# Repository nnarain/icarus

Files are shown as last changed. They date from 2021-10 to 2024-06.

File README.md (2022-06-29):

# Icarus Flight Controller




Icarus is a controller for robotics applications.

Firmware is located [here](https://github.com/nnarain/icarus-firmware).

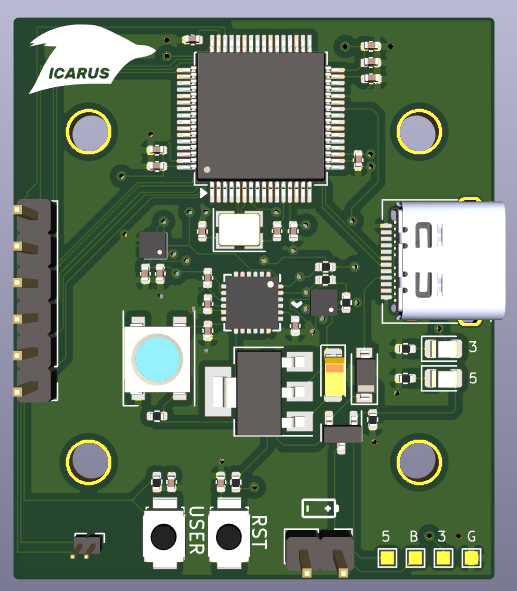
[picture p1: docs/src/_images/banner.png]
Image not found


Features:

* Controls 4 DC brushed motors
* IMU (gyro/accelerometer/temperature)
* Barometer
* USB Serial
* Battery sense
* 30.5 x 30.5 millimeter mounting holes (for drones).

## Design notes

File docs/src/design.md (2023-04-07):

# Design

Below is the design documentation for the Icarus Flight Controller.

Full schematics can be viewed here: {{#find schematic}}

# Scope

The scope of this project is to design and build an embedded system that can be used as a microquad flight controller.

| Priority | Item |
| --- | --- |
| Must | Support control of 4 motors |
| Must | Have motion sensing |
| Must | Interface for remote control |
| Should | Have USB 2.0 support |

# High-level Components

```d2
power: Power Supply {
    usb: USB
    usb.shape: parallelogram

    pwr: PWR Port
    pwr.shape: parallelogram

    reg: Voltage Regulator

    usb -> reg <- pwr
}

sensors: Sensors {
    imu: IMU
    baro: Barometer
    mag: Magnetometer
}

mcu: MCU {
    radio_bus: Radio Bus
    radio_bus.shape: parallelogram

    sensor_bus: Sensor Bus
    sensor_bus.shape: parallelogram

    core: Core
    core.shape: diamond

    pwm: PWM
    pwm.shape: parallelogram

    sensor_bus -> core {
        style.animated: true
    }
    radio_bus -> core {
        style.animated: true
    }
    core -> pwm {
        style.animated: true
    }
}

rf: Radio

rotors: Rotors
rotors.shape: parallelogram

power.reg -> sensors
power.reg -> mcu

rf -> mcu: Throttle {
    style.animated: true
}

mcu -> rf: Telemetry {
    style.animated: true
}

sensors.imu -> mcu: Accel / Gyro {
    style.animated: true
}
sensors.baro -> mcu: Altitude {
    style.animated: true
}
sensors.mag -> mcu: Orientation {
    style.animated: true
}

mcu.pwm -> rotors {
    style.animated: true
}
mcu.pwm -> rotors {
    style.animated: true
}
mcu.pwm -> rotors {
    style.animated: true
}
mcu.pwm -> rotors {
    style.animated: true
}

```

* PWM output to drive rotors
* An IMU can be used for motion sensing. At minimum a gyro and accelerometer would be required
* A magnetometer is needed to prevent yaw drift
* RC input would be require as input to the controller

# Power Supply

**Requirements**

Voltage should be able to handle up to a 3S (11.1V) LiPo for some flexibility in battery choice.

**Power Supply Inputs**

The board will have two inputs for power:

* Two pin input for direct battery connection
* 5V input from a USB connector

# Sensors

**Requirements**

As one of the purposes of this controller is for drones, understanding orientation in the air will be critical.

**Sensor Selection**

* MPU6050 for attitude estimation
* Magnetometer to prevent yaw drift (though not required)
* Barometer for altitude

# MCU

The MCU requirements for this project are pretty basic:

* 4 PWM outputs
* 1x I2C
* USB Serial support

And ESP32-C3-MINI-1 module was selected for the following reasons:

* Enough IO to control 4 motors
* I2C for sensors
* Built-in 2.4GHz radio support + antenna

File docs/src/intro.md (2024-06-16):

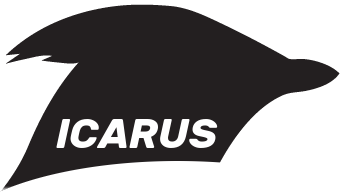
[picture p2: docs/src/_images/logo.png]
image not found!


Icarus is a flight controller for micro-quads.

Features:

* STM32F405 MCU
* IMU (gyro/accelerometer/temperature)
* Magnetometer
* Barometer
* USB 2.0
* 30.5 x 30.5 millimeter mounting pattern

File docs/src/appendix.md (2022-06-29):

# Appendix

| Document  | Item |
| --- | --- |
| Schematic | {{#find schematic}} |
| BOM | {{#find ibom}} |
| Fab Files | {{#find jlcpcb-files}} |

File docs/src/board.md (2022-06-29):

# Board

{{#find schematic-svg}}

{{#find render-top}}

{{#find render-bottom}}

{{#find render-3d}}

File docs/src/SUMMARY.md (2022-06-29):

# Summary

- [Introduction](./intro.md)
- [Design](./design.md)
- [Board](./board.md)
- [Appendix](./appendix.md)

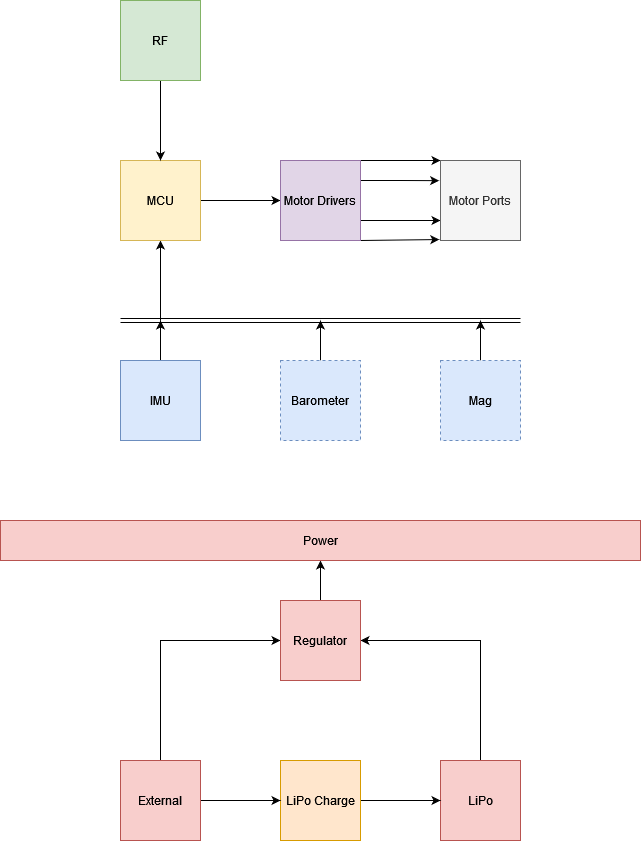
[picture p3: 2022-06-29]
docs/src/_images/highlevel-architecture.png

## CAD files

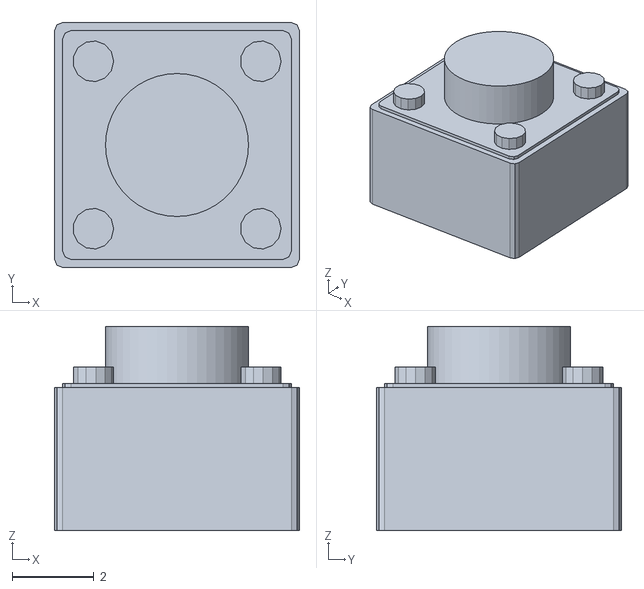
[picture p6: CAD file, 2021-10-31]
hardware/icarus/models/pushbutton_6mm.stl
6.00 x 6.00 x 5.00

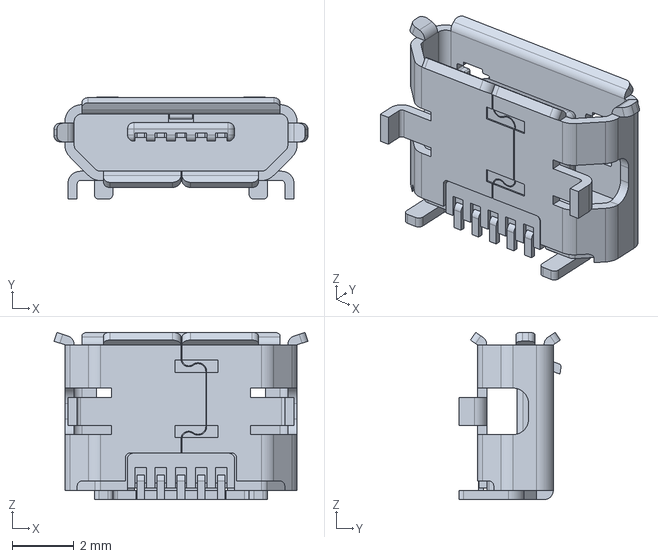
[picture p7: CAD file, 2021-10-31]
hardware/icarus/models/usb-b-micro-1050170001.stp
8.20 x 3.30 x 5.40 mm

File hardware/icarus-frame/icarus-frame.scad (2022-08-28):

// Simple frame for Icarus Flight Controller.
// Not intended to be consider robust (or good for that matter...)

base_dims = [43.084, 36.86, 3];
corners = [
    [base_dims[0] / 2, base_dims[1] / 2, 0],
    [-base_dims[0] / 2, base_dims[1] / 2, 0],
    [-base_dims[0] / 2, -base_dims[1] / 2, 0],
    [base_dims[0] / 2, -base_dims[1] / 2, 0]
];

mounting_hole_radius = 2.125;
mounting_hole_corner_offset = [
    [6.1, 3.429],
    [6.731, 3.429],
    [6.731, 3.175],
    [6.7, 3.1]
];

mounting_hole_positions = [
    [corners[0][0] - mounting_hole_corner_offset[0][0], corners[0][1] - mounting_hole_corner_offset[0][1]],
    [corners[1][0] + mounting_hole_corner_offset[1][0], corners[1][1] - mounting_hole_corner_offset[1][1]],
    [corners[2][0] + mounting_hole_corner_offset[2][0], corners[2][1] + mounting_hole_corner_offset[2][1]],
    [corners[3][0] - mounting_hole_corner_offset[3][0], corners[3][1] + mounting_hole_corner_offset[3][1]]
];

rotor_offsets = [6, 6];

rotor_positions = [
    [corners[0][0] + rotor_offsets[0], corners[0][1] + rotor_offsets[1]],
    [corners[1][0] - rotor_offsets[0], corners[1][1] + rotor_offsets[1]],
    [corners[2][0] - rotor_offsets[0], corners[2][1] - rotor_offsets[1]],
    [corners[3][0] + rotor_offsets[0], corners[3][1] - rotor_offsets[1]],
];

rotor_radius = 3;
rotor_wall_width = 2;
rotor_wall_clearance = 0.4;
rotor_mount_height = 15;
rotor_mount_wire_hole_radius = 2;
rotor_mount_bottom_thickness = 0.8;
rotor_mount_z_offset = 0.3;
strut_length = 10;
strut_thickness = base_dims[2];

battery_dims = [27, 16, 8.5];
battery_carriage_shell_thickness = 3;
battery_carriage_clearance = [1, 1, 2];
battery_carriage_dims = [
    battery_dims[0] + battery_carriage_clearance[0] + battery_carriage_shell_thickness,
    battery_dims[1] + battery_carriage_clearance[1] + battery_carriage_shell_thickness,
    battery_dims[2] + battery_carriage_clearance[2] + battery_carriage_shell_thickness
];
battery_cutout_dims = [
    battery_dims[0] + battery_carriage_clearance[0],
    battery_dims[1] + battery_carriage_clearance[1],
    battery_dims[2] + battery_carriage_clearance[2]
];

rotor_mount_radius = rotor_radius + rotor_wall_clearance + rotor_wall_width;


d = 0.01;

module rotor_mount() {
    z_offset = rotor_mount_z_offset * rotor_mount_height;

    difference() {
        union() {
            // Base rotor motor shape
            translate([0, 0, -z_offset]) 
                cylinder(r=rotor_mount_radius, h=rotor_mount_height, center=true, $fn=50);
            // Connective part of the main body
            translate([-strut_length / 2, 0, 0])
                cube(size=[strut_length, rotor_radius, strut_thickness], center=true);
        }
        union() {
            // Cutout space for the rotor
            translate([0, 0, rotor_mount_bottom_thickness - z_offset])
                cylinder(r=rotor_radius + rotor_wall_clearance, h=rotor_mount_height, center=true, $fn=50);
            translate([0, 0, -rotor_mount_height / 2 + d - z_offset])
                cylinder(r=rotor_mount_wire_hole_radius, h=rotor_mount_bottom_thickness * 2, center=true, $fn=100);
        }
    }
}

module battery_carriage() {
    difference() {
        cube(size=battery_carriage_dims, center=true);
        translate([battery_carriage_dims[0] / 2, 0, -d])
            cube(size=[battery_cutout_dims[0] * 2, battery_cutout_dims[1], battery_cutout_dims[2]], center=true);
    }
}

module base() {
    difference() {
        cube(size=base_dims, center=true);

        for (p = mounting_hole_positions) {
            translate([p[0], p[1], 0])
                cylinder(r=mounting_hole_radius, h=base_dims[2] * 2, center=true, $fn=100);
        }
    }
}

module frame() {
    union() {
        // Base where the controller is mounted
        base();

        // Battery Carriage
        translate([0, 0, -battery_carriage_dims[2] + battery_carriage_dims[2] / 2])
            battery_carriage();

        // Position rotor mounts
        for (i = [0:3]) {
            pos = rotor_positions[i];
            translate([pos[0], pos[1], 0])
                rotate([0, 0, 45 + (90 * i)])
                    rotor_mount();
        }
    }
    // rotor_mount();
}

frame();

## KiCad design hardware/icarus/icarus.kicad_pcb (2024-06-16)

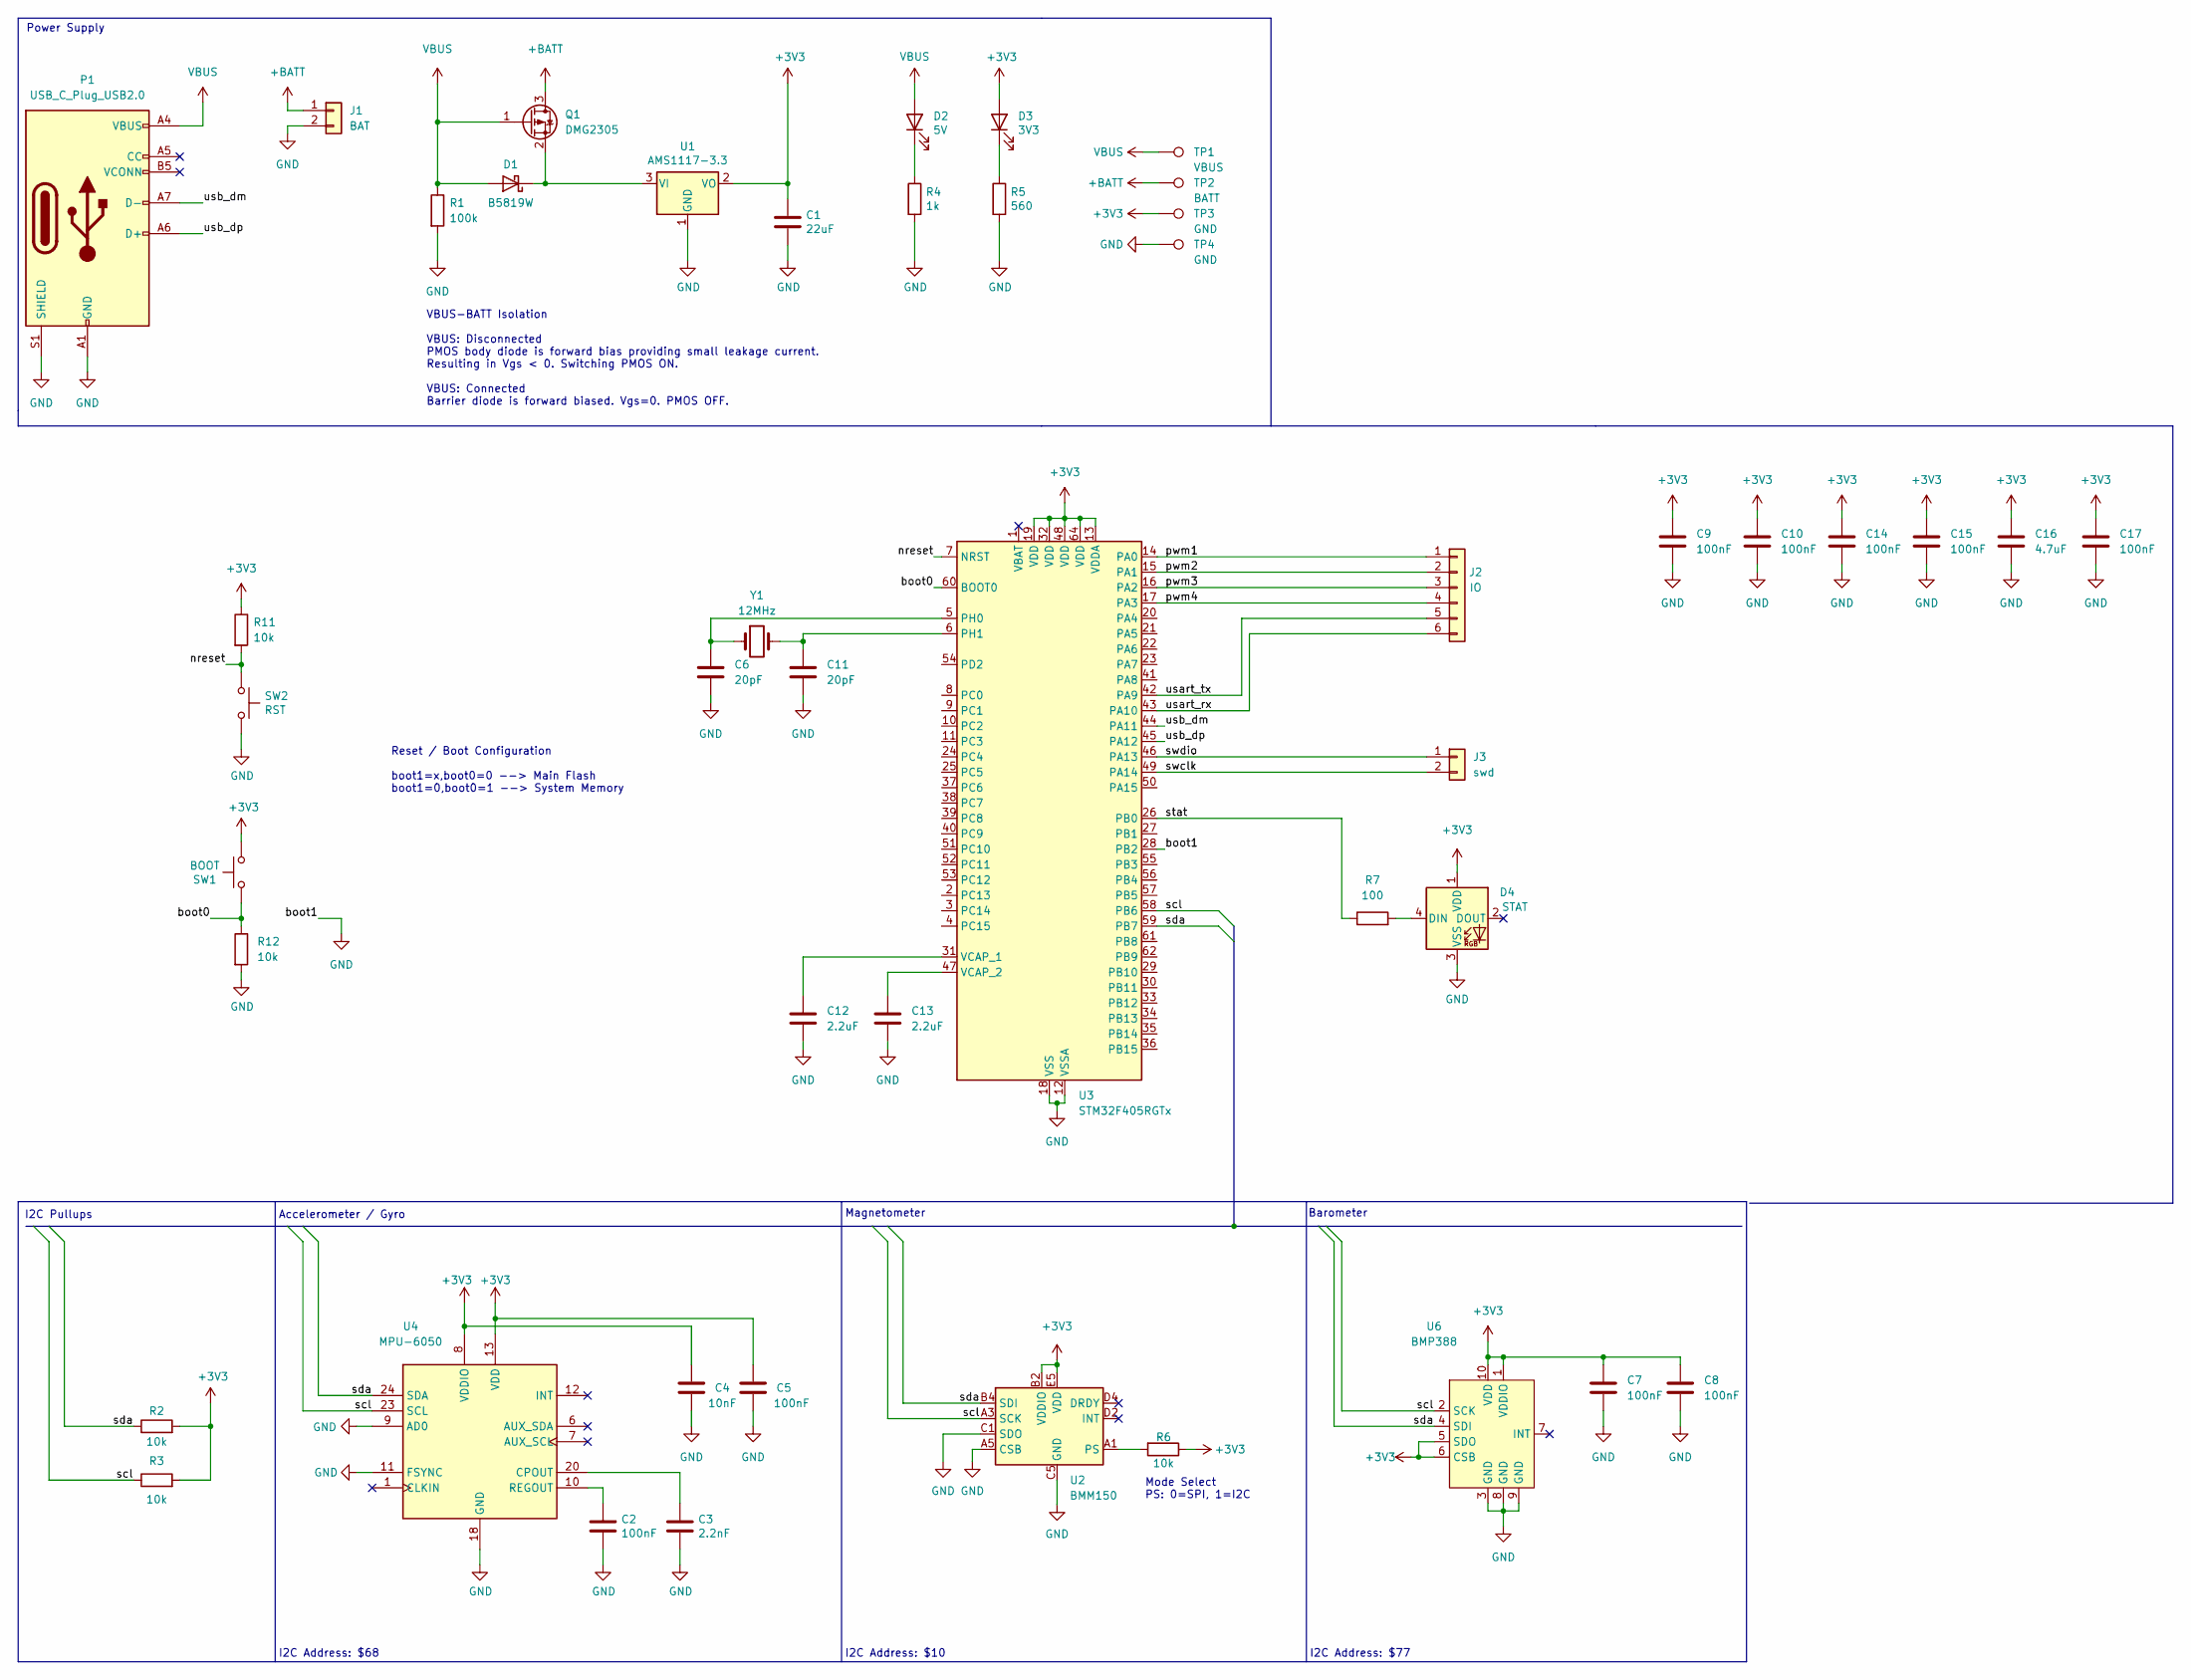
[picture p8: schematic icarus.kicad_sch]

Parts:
C1: 22uF; CP_EIA-3216-18_Kemet-A; LCSC C116575
C2, C5, C7, C8, C9, C10, C14, C15, C17: 100nF; C_0402_1005Metric; LCSC C307331
C3: 2.2nF; C_0402_1005Metric; LCSC C1531
C4: 10nF; C_0402_1005Metric; LCSC C15195
C6, C11: 20pF; C_0402_1005Metric; LCSC C1554
C12, C13: 2.2uF; C_0402_1005Metric; LCSC C12530
C16: 4.7uF; C_0402_1005Metric; LCSC C23733
D1: B5819W; D_SOD-123; LCSC C8598
D2: 5V; LED_0805_2012Metric; LCSC C434432
D3: 3V3; LED_0805_2012Metric; LCSC C434432
D4: STAT; LED_WS2812B_PLCC4_5.0x5.0mm_P3.2mm; LCSC C2761795
J1: BAT; PinHeader_1x02_P2.54mm_Vertical
J2: IO; PinHeader_1x06_P2.54mm_Vertical
J3: swd; PinHeader_1x02_P1.00mm_Vertical
P1: USB_C_Plug_USB2.0; TYPE-C-31-M-04; LCSC C129018
Q1: DMG2305; SOT-23; LCSC C150470
R1: 100k; R_0402_1005Metric; LCSC C25741
R2, R3, R6, R11, R12: 10k; R_0402_1005Metric; LCSC C25744
R4: 1k; R_0402_1005Metric; LCSC C25543
R5: 560; R_0402_1005Metric; LCSC C25172
R7: 100; R_0402_1005Metric; LCSC C25076
SW1: BOOT; TS-1088-AR02016; LCSC C720477
SW2: RST; TS-1088-AR02016; LCSC C720477
TP1: VBUS; TestPoint_Pad_1.0x1.0mm
TP2: BATT; TestPoint_Pad_1.0x1.0mm
TP3, TP4: GND; TestPoint_Pad_1.0x1.0mm
U1: AMS1117-3.3; SOT-223-3_TabPin2; LCSC C6186
U2: BMM150; WLCSP-12_1.56x1.56mm_P0.4mm; LCSC C171681
U3: STM32F405RGTx; LQFP-64_10x10mm_P0.5mm
U4: MPU-6050; InvenSense_QFN-24_4x4mm_P0.5mm; LCSC C24112
U6: BMP388; LCSC C779278
Y1: 12MHz; Crystal_SMD_3225-4Pin_3.2x2.5mm; LCSC C9002

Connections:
+3V3: C1.1, C4.2, C5.2, C7.1, C8.1, C9.1, C10.1, C14.1, C15.1, C16.1, C17.1, D3.2 (A), D4.1 (VDD), R2.2, R3.2, R6.1, R11.1, SW1.2, TP3.1, U1.2 (VO), U2.B2 (VDDIO), U2.E5 (VDD), U3.13 (VDDA), U3.19 (VDD), U3.32 (VDD), U3.48 (VDD), U3.64 (VDD), U4.8 (VDDIO), U4.13 (VDD), U6.1 (VDDIO), U6.5 (SDO), U6.6 (CSB), U6.10 (VDD)
+BATT: J1.1, Q1.3 (D), TP2.1
/boot0: R12.1, SW1.1, U3.60 (BOOT0)
/nreset: R11.2, SW2.1, U3.7 (NRST); also elsewhere on the board
/pwm1: J2.1, U3.14 (PA0)
/pwm2: J2.2, U3.15 (PA1)
/pwm3: J2.3, U3.16 (PA2)
/pwm4: J2.4, U3.17 (PA3)
/scl: R3.1, U2.A3 (SCK), U3.58 (PB6), U4.23 (SCL), U6.2 (SCK)
/sda: R2.1, U2.B4 (SDI), U3.59 (PB7), U4.24 (SDA), U6.4 (SDI)
/stat: R7.1, U3.26 (PB0)
/swclk: J3.2, U3.49 (PA14)
/swdio: J3.1, U3.46 (PA13)
/usart_rx: J2.6, U3.43 (PA10)
/usart_tx: J2.5, U3.42 (PA9)
/usb_dm: P1.A7 (D-), U3.44 (PA11)
/usb_dp: P1.A6 (D+), U3.45 (PA12)
GND: C1.2, C2.2, C3.2, C4.1, C5.1, C6.2, C7.2, C8.2, C9.2, C10.2, C11.2, C12.2, C13.2, C14.2, C15.2, C16.2, C17.2, D4.3 (VSS), J1.2, P1.A1 (GND), P1.A12 (GND), P1.B1 (GND), P1.B12 (GND), P1.S1 (SHIELD), R1.2, R4.2, R5.2, R12.2, SW2.2, TP4.1, U1.1 (GND), U2.A5 (CSB), U2.C1 (SDO), U2.C5 (GND), U2.E1 (GND), U2.E3 (GND), U3.12 (VSSA), U3.18 (VSS), U3.28 (PB2), U3.63 (VSS), U4.9 (AD0), U4.11 (FSYNC), U4.18 (GND), U6.3 (GND), U6.8 (GND), U6.9 (GND); also elsewhere on the board
unnamed: D1.1 (K), Q1.2 (S), U1.3 (VI)
unnamed: D2.1 (K), R4.1
unnamed: D3.1 (K), R5.1
unnamed: D4.4 (DIN), R7.2
unnamed: R6.2, U2.A1 (PS)
unnamed: C6.1, U3.5 (PH0), Y1.1
unnamed: C11.1, U3.6 (PH1), Y1.2
unnamed: C12.1, U3.31 (VCAP_1)
unnamed: C13.1, U3.47 (VCAP_2)
unnamed: C3.1, U4.20 (CPOUT)
unnamed: C2.1, U4.10 (REGOUT)
VBUS: D1.2 (A), D2.2 (A), P1.A4 (VBUS), P1.A9 (VBUS), P1.B4 (VBUS), P1.B9 (VBUS), Q1.1 (G), R1.1, TP1.1

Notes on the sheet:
I2C Address: $77
Barometer
I2C Address: $68
I2C Address: $10
I2C Pullups
VBUS-BATT Isolation VBUS: Disconnected PMOS body diode is forward bias providing small leakage current. Resulting in Vgs < 0. Switching PMOS ON. VBUS: Connected Barrier diode is forward biased. Vgs=0. PMOS OFF.
Accelerometer / Gyro
Mode Select PS: 0=SPI, 1=I2C
Magnetometer
Reset / Boot Configuration boot1=x,boot0=0 --> Main Flash boot1=0,boot0=1 --> System Memory
Power Supply

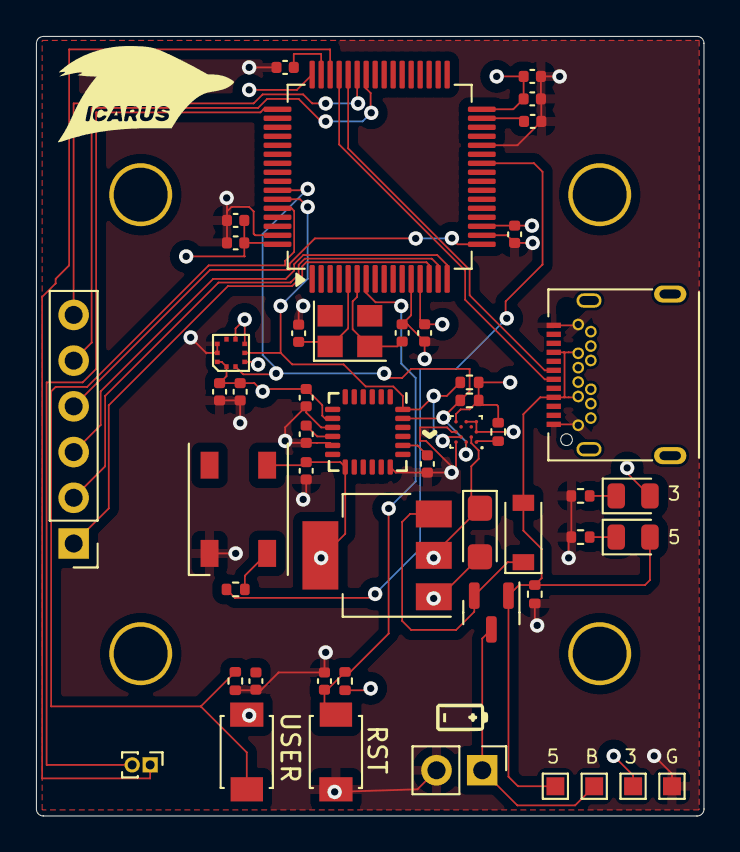
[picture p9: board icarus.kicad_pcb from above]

Board: 4 copper layers, 37.1 x 43.3 mm, 49 parts (0 on the bottom side), 30 nets.

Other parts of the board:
C9#2, C10#2: 100nF; C_0402_1005Metric

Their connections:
/nreset: C9#2.1; also elsewhere on the board
GND: C9#2.2, C10#2.2; also elsewhere on the board

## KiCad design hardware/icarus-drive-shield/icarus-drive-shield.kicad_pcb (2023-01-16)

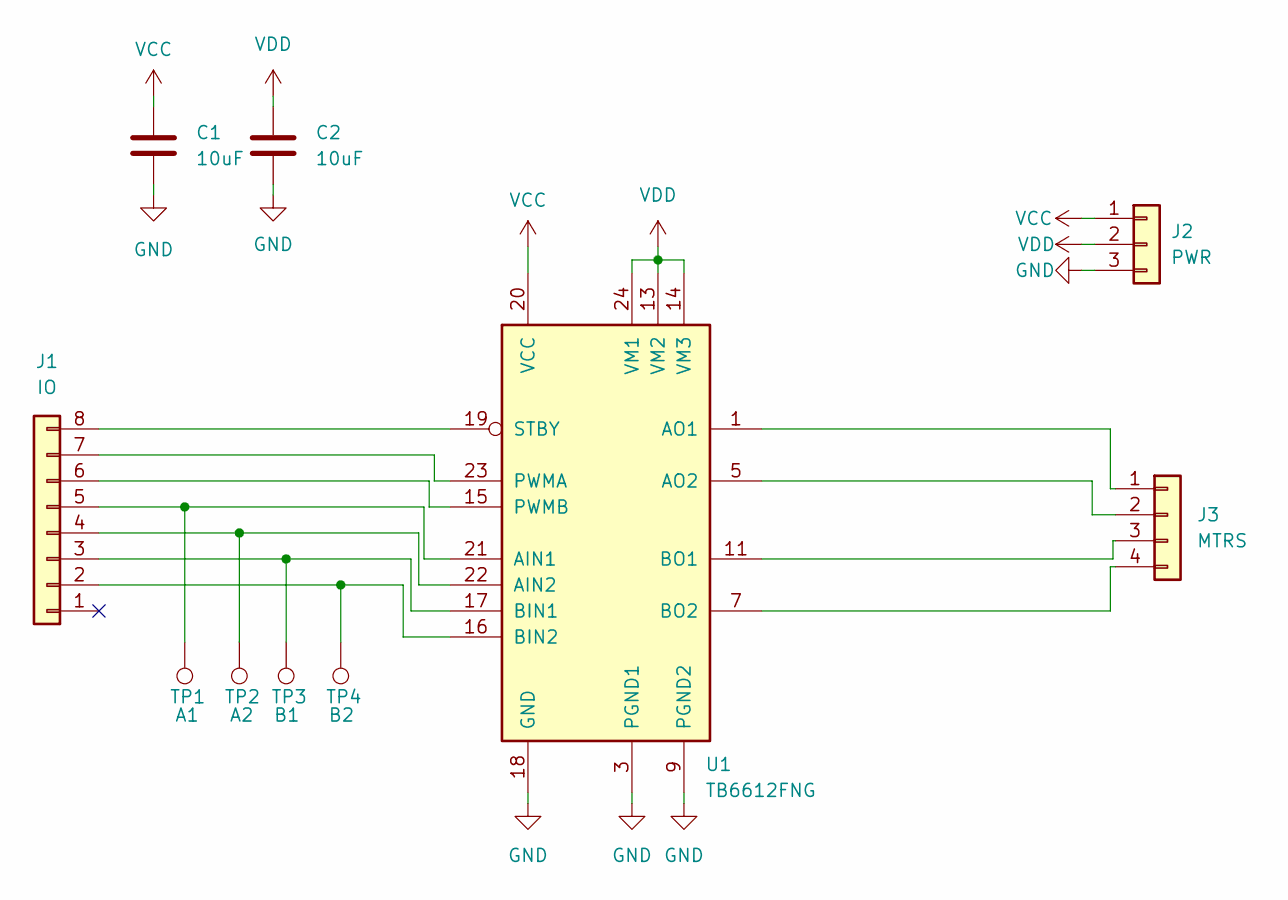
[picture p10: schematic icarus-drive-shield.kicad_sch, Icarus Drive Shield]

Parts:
C1, C2: 10uF; C_0805_2012Metric; LCSC C440198
J1: IO; PinHeader_1x08_P2.54mm_Vertical
J2: PWR; PinHeader_1x03_P2.54mm_Vertical
J3: MTRS; PinHeader_1x04_P2.54mm_Vertical
TP1: A1; TestPoint_Pad_2.0x2.0mm
TP2: A2; TestPoint_Pad_2.0x2.0mm
TP3: B1; TestPoint_Pad_2.0x2.0mm
TP4: B2; TestPoint_Pad_2.0x2.0mm
U1: TB6612FNG; SSOP-24_5.3x8.2mm_P0.65mm; LCSC C88224

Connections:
GND: C1.2, C2.2, J2.3, U1.3 (PGND1), U1.4 (PGND1), U1.9 (PGND2), U1.10 (PGND2), U1.18 (GND)
unnamed 1: J1.2, TP4.1, U1.16 (BIN2); also elsewhere on the board
unnamed 2: J1.3, TP3.1, U1.17 (BIN1); also elsewhere on the board
unnamed 3: J1.4, TP2.1, U1.22 (AIN2); also elsewhere on the board
unnamed 7: J1.8, U1.19 (STBY); also elsewhere on the board
unnamed: J3.1, U1.1 (AO1), U1.2 (AO1)
unnamed: J3.2, U1.5 (AO2), U1.6 (AO2)
unnamed: J3.4, U1.7 (BO2), U1.8 (BO2)
unnamed: J3.3, U1.11 (BO1), U1.12 (BO1)
unnamed: J1.6, U1.15 (PWMB)
unnamed: J1.5, TP1.1, U1.21 (AIN1)
unnamed: J1.7, U1.23 (PWMA)
VCC: C1.1, J2.1, U1.20 (VCC)
VDD: C2.1, J2.2, U1.13 (VM2), U1.14 (VM3), U1.24 (VM1)

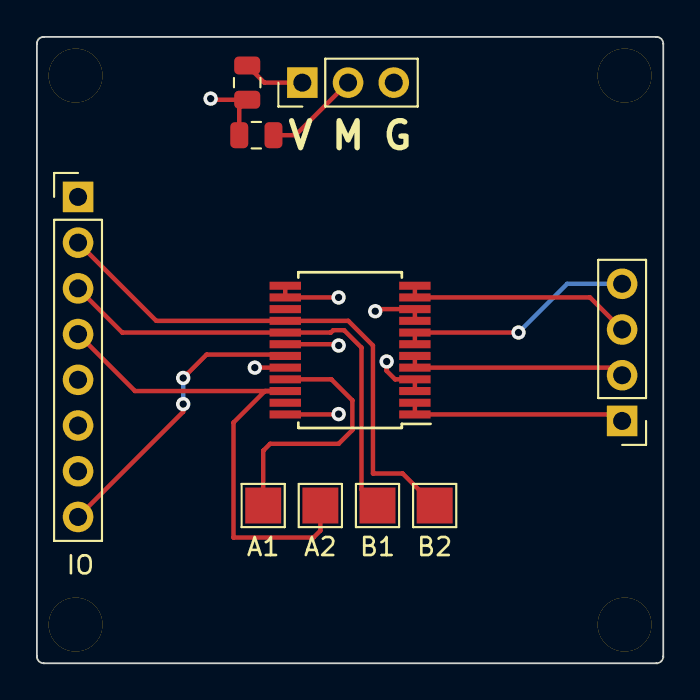
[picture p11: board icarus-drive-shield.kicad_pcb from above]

Board: 4 copper layers, 34.8 x 34.8 mm, 10 parts (0 on the bottom side), 12 nets.

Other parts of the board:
IO: IO; PinHeader_1x08_P2.54mm_Vertical

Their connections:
unnamed 1: IO.2; also elsewhere on the board
unnamed 2: IO.3; also elsewhere on the board
unnamed 3: IO.4; also elsewhere on the board
unnamed 7: IO.8; also elsewhere on the board

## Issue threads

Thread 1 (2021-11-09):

Fix USB connector footprint

nnarain, 2021-11-09:
Selected footprint did not pass JLCPCB inspection.

Closed 2022-02-13.

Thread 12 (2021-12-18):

Reset Monitor / Watchdog

nnarain, 2021-12-18:
Add a reset monitor IC to hold the MCU in reset until the correct logic voltage level is reached. Some of these ICs come with a watch mechanism built in to reset the MCU if an IO line was not toggled within a timeout window.

Closed 2022-06-29.

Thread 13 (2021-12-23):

Select a smaller 3.3V regulator

nnarain, 2021-12-23:
AMS1117-3.3 was picked for availability. It can output ~800mA, which is unnecessary. A smaller regulator could be selected to reduce the amount of space used on the board.

Closed 2022-02-13.

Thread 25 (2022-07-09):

Move stat led to another pin

nnarain, 2022-07-09:
Initial printing of device info that the esp does at start up causes the stat led to go full brightness. Application firmware will immediately change it, but would be better if it was not on the serial tx pin.

Closed 2023-02-12.

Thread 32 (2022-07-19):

Battery sense may not work with LiPo in place

nnarain, 2022-07-19:
Looks like it is always applying a voltage to BATT.

Closed 2023-02-12.

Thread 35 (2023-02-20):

Consider a different mounting pattern

nnarain, 2023-02-20:
30.5mm is less common on micro quad frames it seems

Options

- 20.5mm
- 25.5mm
- 30.5mm

nnarain, 2023-02-21:
More 4-in-1 ESCs are available in 20x20 then 25x25.

Closed 2024-07-03.

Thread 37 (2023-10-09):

Advanced telemetry output

nnarain, 2023-10-09:
Dedicate output for advance telemetry

* Attitude / Orientation
* Internal State
* Raw sensor data

Maybe dedicated SPI pin

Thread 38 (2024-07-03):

Consider removing USB Connector

nnarain, 2024-07-03:
This take up space on the board but is only used for flashing. Flashing over UART or just the SWD interface is also an option.

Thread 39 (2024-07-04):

Replace ws2812 led with normal led

nnarain, 2024-07-04:
Keep it simple.

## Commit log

2021-11-06 Design with stm32f3
    [icarus.kicad_pcb, icarus.sch]
2021-11-06 Switch linear regulator
    [icarus.kicad_pcb, icarus.sch]
2021-12-03 Layer update
    [icarus.kicad_pcb]
2021-12-04 Resolves #2, #9, #10. Test points, USART1 Labels, IMU AD0 pint.
    [icarus.kicad_pcb, icarus.sch]
2021-12-04 Resolves #4. Increased resistor values for LEDs
    [icarus.sch]
2022-01-28 Kicad 6 Update
    [icarus.kicad_pcb, icarus.kicad_sch]
2022-01-30 Resolves #3, #13. Use 5 pin header for SWD, Use SOT-89 package for regulator.
    [icarus.kicad_sch]
2022-01-30 Resolves #5. Smaller push buttons for BOOT and RST
    [icarus.kicad_sch]
2022-01-30 Resolves #1. Micro USB footprint selection
    [icarus.kicad_sch]
2022-02-10 Resolves #6, #17, #18. Resize and routing. Added barometer.
    [icarus.kicad_pcb, icarus.kicad_sch]
2022-02-12 Added LCSC to BMP on schematic
    [icarus.kicad_sch]
2022-02-22 Resolves #8. KiCAD CI
    [icarus.kicad_sch]
2022-04-07 Resolves #20. BoM for JLCPCB
2022-06-16 Update kicad-inventory
2022-06-29 Rev C
    [icarus.kicad_pcb, icarus.kicad_sch]
2022-08-08 Initial frame design
    [icarus-frame.scad]
2022-08-28 Adjust frame values
    [icarus-frame.scad]
2023-01-16 Drive shield
    [icarus-drive-shield.kicad_pcb, icarus-drive-shield.kicad_sch]
2023-01-26 Rev D
    [icarus.kicad_pcb, icarus.kicad_sch]
2023-04-19 Rev D.2
    [icarus.kicad_pcb]
2023-10-06 kicad 7
    [icarus.kicad_pcb, icarus.kicad_sch]
2024-06-16 Update actions
    [icarus.kicad_pcb, icarus.kicad_sch]
2024-06-16 add stm32 lcsc number
    [icarus.kicad_sch]
